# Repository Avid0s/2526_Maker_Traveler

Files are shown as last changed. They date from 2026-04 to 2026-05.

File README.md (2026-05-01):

# 25-26_Maker_Traveler
Gabriel VIDON\
Projet d'option Maker à l'ENSEA.

# Vidéo :
Version 1 min 30 :\
https://youtu.be/IOBbxCDs6Es

Version 1 min 45 : (une étape en plus)\
https://youtu.be/CtQkx19j3xo

# 1 Description du projet

## 1.1 Contexte

J'ai toujours été passioné par la robotique et les systèmes embarqués, c'est pour cela que dans le cadre d'un projet Maker qui devait regrouper le plus de technologies possibles pour apprendre leur fonctionnement. J'ai décidé de travailler sur un projet de voiture téléguidée par connection bluetooth. Pour éviter de devoir créer un système de rotation pour les roues de zero, j'ai décidé d'utiliser des roues holonomes.\ 
Ce système qui deverait toucher à toutes les technologies d'impression 3D, de découpe laser, routage pcb, et toutes les autres vues en cours de Maker.
Mes objectifs sont les suivants :
- Créer un chassis pouvant supporter l'ensemble du système
- Créer un PCB avec un ESP32 permettant de controler les moteurs
- Créer un programme permettant de communiquer en bluetooth avec l'ESP et de controler la voiture depuis un telephone puis une manette.

## 1.2 Retroplanning

| Séance | Objectif|
|---|---|
|TP1 |Définir les spécifications, choisir les composants, rédiger le cahier des charges et planifier les tâches.|
|TP2 |Modéliser le châssis en 3D, concevoir le schéma du PCB et préparer les fichiers pour la fabrication.|
|TP3 |Imprimer/découper le châssis, finaliser le PCB et préparer les outils pour la séance suivante.|
|TP4 |Souder les composants sur le PCB et écrire le code de base pour contrôler les moteurs.|
|TP5 |Développer la communication Bluetooth et tester les mouvements de la voiture.|
|TP6 |Assembler le châssis, tester l'ensemble (mouvements, Bluetooth) et finaliser le code.|
|TP7 |Valider les tests, rédiger le rapport technique et préparer la démonstration.|

# 2 Projet

## Séance 1

L'alimentation de la voiture sera fait grâce a une batterie 12v, cette tension sera convertie en 5v par un convertisseur DC-DC, qui alimentera toute la carte.\
Un esp32 recuperera les informations de mouvement depuis une connection bluetooth, enverra la PWM appropriée aux drivers, qui eux controleront les moteurs.\
Les moteurs seront eux alimentés par la batterie 12v, et leur valeur d'encodeur sera renvoyée à l'esp pour permettre un niveau de précision adéquat pour utiliser les roues omnidirectionelles.\
Une interface sera faite sur telephone avec l'application BT electronics, et si le temps le permets, le robot sera controlé par une manette de ps4

| Composant | Référence | Lien | Quantité |
|---|---|---|---|
| Moteurs | FIT0520 | [https://www.dfrobot.com/product-1619.html](https://www.dfrobot.com/product-1619.html)| x4 |
| Drivers moteur | DRV8411APWPR | | x2 |
| ESP32 | | | x1 |
| Roues omnidirectionelles | FIT0779 | [https://www.gotronic.fr/art-roue-omnidirectionnelle-droite-fit0780-34179.htm](https://www.gotronic.fr/art-roue-omnidirectionnelle-droite-fit0780-34179.htm) | x2L x2R |
| Convertisseur 6v-5v | 171013801 | [https://www.we-online.com/components/products/datasheet/171013801.pdf](https://www.we-online.com/components/products/datasheet/171013801.pdf) | x1 |
| Batterie 6v | fait in ensea |  | x1 |

Lien Onshape :\
[https://cad.onshape.com/documents/018aeca4da422949587763ea/w/2b34d823b7b37a4e9442f19b/e/016c48b2dd776d725fede060](https://cad.onshape.com/documents/018aeca4da422949587763ea/w/2b34d823b7b37a4e9442f19b/e/016c48b2dd776d725fede060)

traveler

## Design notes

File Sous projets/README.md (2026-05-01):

# Onshape CAD
screw_box_thing
phone_holder
spring
joint_thing
useless_box

# Impression 3D
Weaponised_benchy

# Découpe laser
https://github.com/user-attachments/assets/71cb4131-c118-4ef8-b6b2-2d7144401bef

# Routage PCB
Je me rappelle d'avoir fait la majorité du travail demandé pour cet exercice, mais je ne retrouve pas le document KiCad. Je peux en échange vous montrer d'autres projets KiCad que j'ai faits depuis.

https://github.com/Spoyke/Nomad/tree/main/PCBs/Commande
schema_elec_nomad
routage_nomad
Voici la version finale de mon PCB de projet de 2A, qui a été refait à plusieurs reprises.

https://github.com/Avid0s/2526_Maker_Traveler/tree/main/PCB/Traveler_v2
Vous pouvez aussi voir mon PCB de ce projet sur ce git

Et même le routage que j'ai fait durant mon stage de BUT2
Zuken_CR-5000
Zuken_CR-5000_part2
L'application utilisée est [CR-5000 de Zuken](https://en.wikipedia.org/wiki/CR-5000)

# Soudure PCB
Nous n'avons pas pris de photos du PCB et nous ne le retrouvons plus maintenant :(

# Couture
Couture_v1
Couture_v2

# Batteries
Je n'ai pas pris de photos de la batterie non plus. J'avais fait une batterie 3s 2p et c'est celle qui a cramé dans la boite.

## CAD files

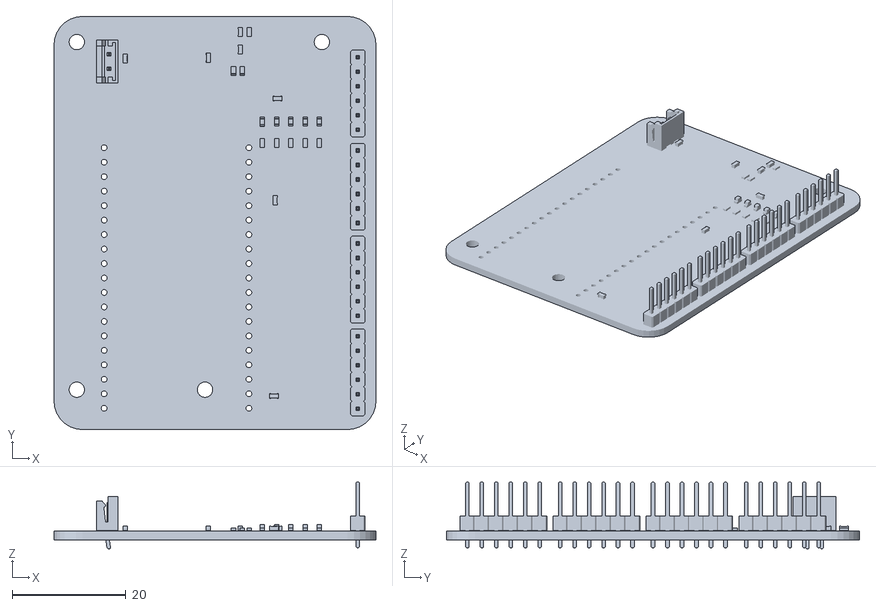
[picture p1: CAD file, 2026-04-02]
PCB/Traveler_v2/Traveler.stl
56.5 x 72.5 x 11.7

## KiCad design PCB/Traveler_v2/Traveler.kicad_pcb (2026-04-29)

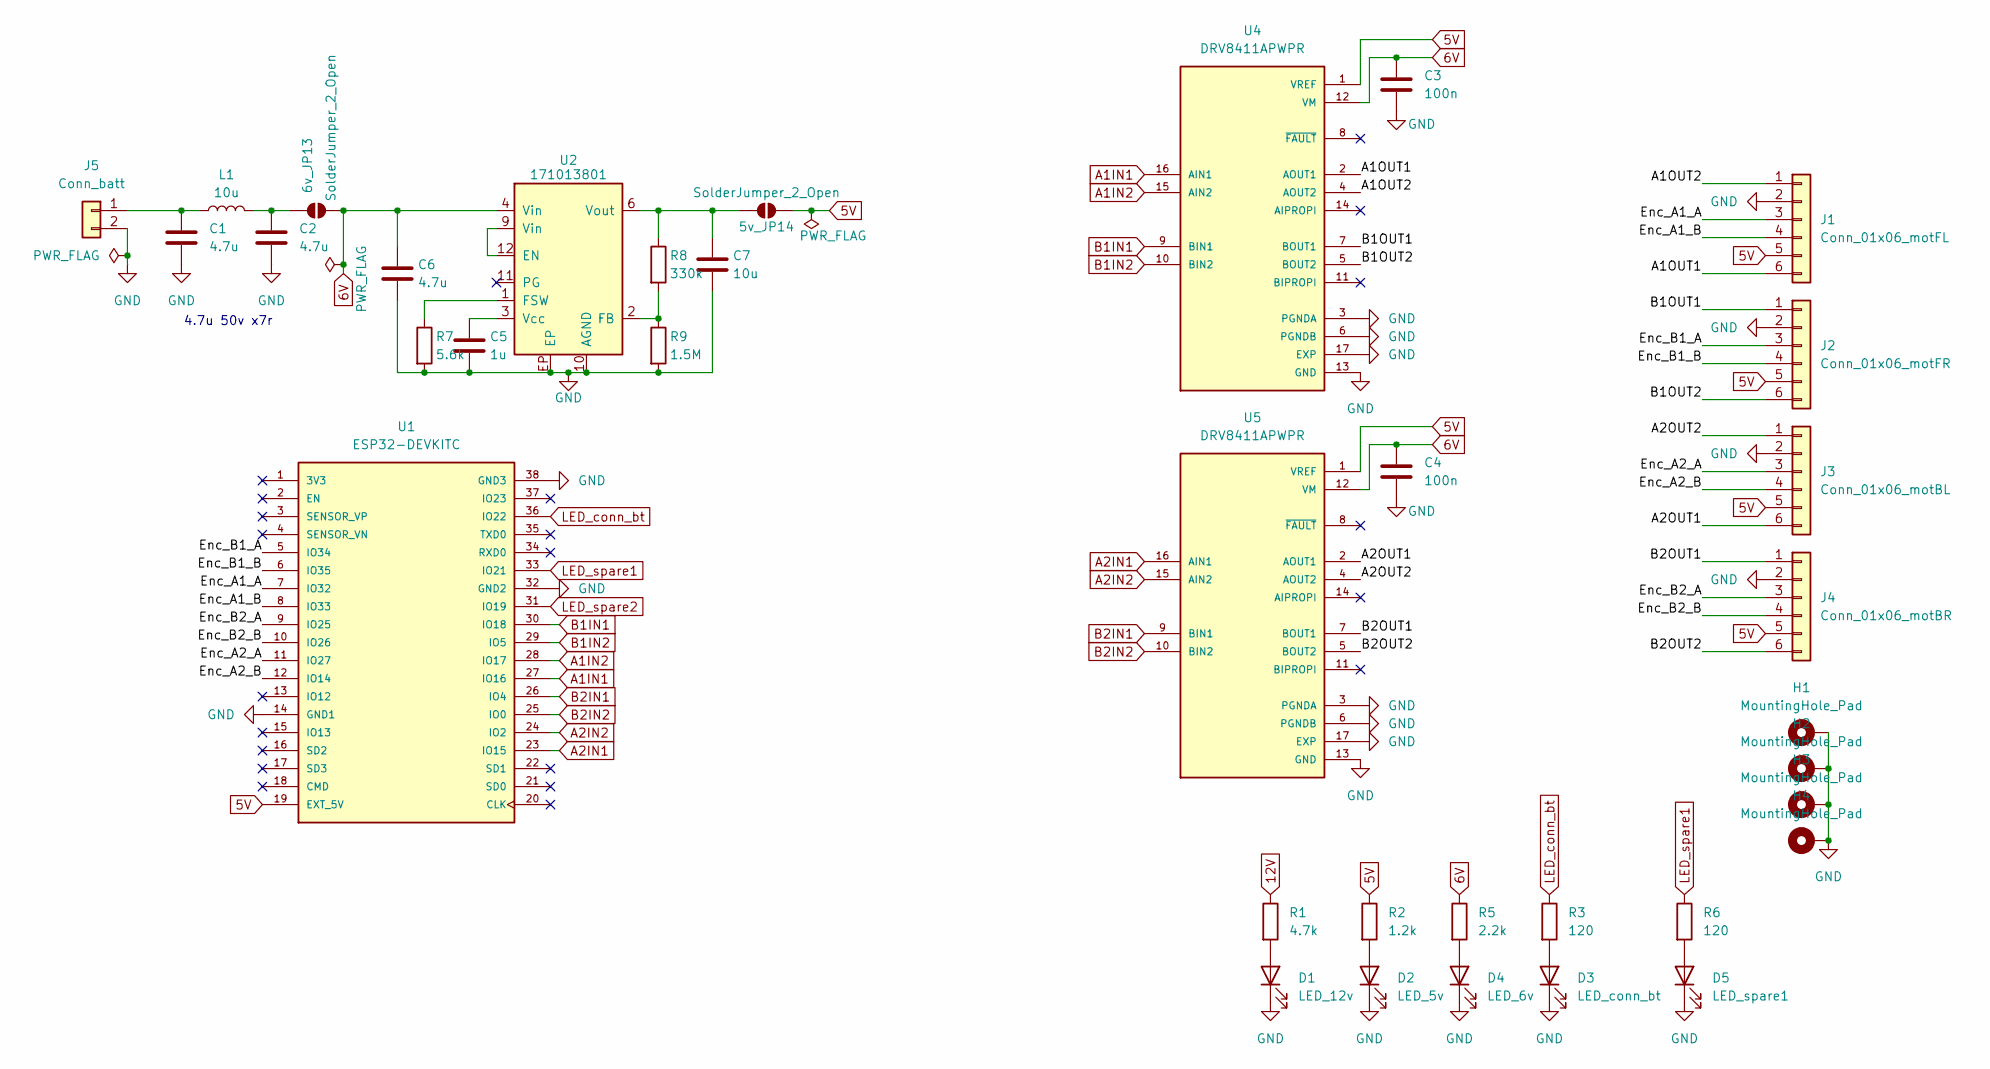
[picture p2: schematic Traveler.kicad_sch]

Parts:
5v_JP14, 6v_JP13: SolderJumper_2_Open; SolderJumper-2_P1.3mm_Open_TrianglePad1.0x1.5mm
C1, C2, C6: 4.7u; C_0603_1608Metric
C3, C4: 100n; C_0603_1608Metric
C5: 1u; C_0603_1608Metric
C7: 10u; C_0603_1608Metric
D1: LED_12v; LED_0603_1608Metric_Pad1.05x0.95mm_HandSolder
D2: LED_5v; LED_0603_1608Metric_Pad1.05x0.95mm_HandSolder
D3: LED_conn_bt; LED_0603_1608Metric_Pad1.05x0.95mm_HandSolder
D4: LED_6v; LED_0603_1608Metric_Pad1.05x0.95mm_HandSolder
D5: LED_spare1; LED_0603_1608Metric_Pad1.05x0.95mm_HandSolder
H1, H2, H3, H4: MountingHole_Pad; MountingHole_2.7mm_Pad_TopBottom
J1: Conn_01x06_motFL; PinHeader_1x06_P2.54mm_Vertical
J2: Conn_01x06_motFR; PinHeader_1x06_P2.54mm_Vertical
J3: Conn_01x06_motBL; PinHeader_1x06_P2.54mm_Vertical
J4: Conn_01x06_motBR; PinHeader_1x06_P2.54mm_Vertical
J5: Conn_batt; JST_EH_B2B-EH-A_1x02_P2.50mm_Vertical
L1: 10u; capa1
R1: 4.7k; R_0603_1608Metric
R2: 1.2k; R_0603_1608Metric
R3, R6: 120; R_0603_1608Metric
R5: 2.2k; R_0603_1608Metric
R7: 5.6k; R_0603_1608Metric
R8: 330k; R_0603_1608Metric
R9: 1.5M; R_0603_1608Metric
U1: ESP32-DEVKITC; MODULE_ESP32-DEVKITC; PARTREV N/A
U2: 171013801; WPME-VDLM_LGA-12EP
U4, U5: DRV8411APWPR; IC_DRV8411APWPR; PARTREV A

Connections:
5V: 5v_JP14.2 (B), J1.5, J2.5, J3.5, J4.5, R2.1, U1.19 (EXT_5V), U4.1 (VREF), U5.1 (VREF)
6V: 6v_JP13.2 (B), C3.1, C4.1, C6.1, R5.1, U2.4 (Vin), U2.5 (Vin), U4.12 (VM), U5.12 (VM)
12V: R1.1
/A1OUT1: J1.6, U4.2 (AOUT1)
/A1OUT2: J1.1, U4.4 (AOUT2)
/A2OUT1: J3.6, U5.2 (AOUT1)
/A2OUT2: J3.1, U5.4 (AOUT2)
/B1OUT1: J2.1, U4.7 (BOUT1)
/B1OUT2: J2.6, U4.5 (BOUT2)
/B2OUT1: J4.1, U5.7 (BOUT1)
/B2OUT2: J4.6, U5.5 (BOUT2)
/Enc_A1_A: J1.3, U1.7 (IO32)
/Enc_A1_B: J1.4, U1.8 (IO33)
/Enc_A2_A: J3.3, U1.11 (IO27)
/Enc_A2_B: J3.4, U1.12 (IO14)
/Enc_B1_A: J2.3, U1.5 (IO34)
/Enc_B1_B: J2.4, U1.6 (IO35)
/Enc_B2_A: J4.3, U1.9 (IO25)
/Enc_B2_B: J4.4, U1.10 (IO26)
A1IN1: U1.27 (IO16), U4.16 (AIN1)
A1IN2: U1.28 (IO17), U4.15 (AIN2)
A2IN1: U1.23 (IO15), U5.16 (AIN1)
A2IN2: U1.24 (IO2), U5.15 (AIN2)
B1IN1: U1.30 (IO18), U4.9 (BIN1)
B1IN2: U1.29 (IO5), U4.10 (BIN2)
B2IN1: U1.26 (IO4), U5.9 (BIN1)
B2IN2: U1.25 (IO0), U5.10 (BIN2)
GND: C1.2, C2.2, C3.2, C4.2, C5.2, C6.2, C7.2, D1.1 (K), D2.1 (K), D3.1 (K), D4.1 (K), D5.1 (K), H1.1, H2.1, H3.1, H4.1, J1.2, J2.2, J3.2, J4.2, J5.2, R7.2, R9.2, U1.14 (GND1), U1.32 (GND2), U1.38 (GND3), U2.10 (AGND), U2.EP, U4.3 (PGNDA), U4.6 (PGNDB), U4.13 (GND), U4.17 (EXP), U5.3 (PGNDA), U5.6 (PGNDB), U5.13 (GND), U5.17 (EXP)
LED_conn_bt: R3.1, U1.36 (IO22)
LED_spare1: R6.1, U1.33 (IO21)
LED_spare2: U1.31 (IO19)
unnamed: 6v_JP13.1 (A), C2.1, L1.2
unnamed: D1.2 (A), R1.2
unnamed: D2.2 (A), R2.2
unnamed: D3.2 (A), R3.2
unnamed: D4.2 (A), R5.2
unnamed: D5.2 (A), R6.2
unnamed: C1.1, J5.1, L1.1
unnamed: U2.9 (Vin), U2.12 (EN)
unnamed: R8.2, R9.1, U2.2 (FB)
unnamed: R7.1, U2.1 (FSW)
unnamed: C5.1, U2.3 (Vcc)
Vout: 5v_JP14.1 (A), C7.1, R8.1, U2.6 (Vout), U2.7 (Vout)

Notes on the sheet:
4.7u 50v x7r

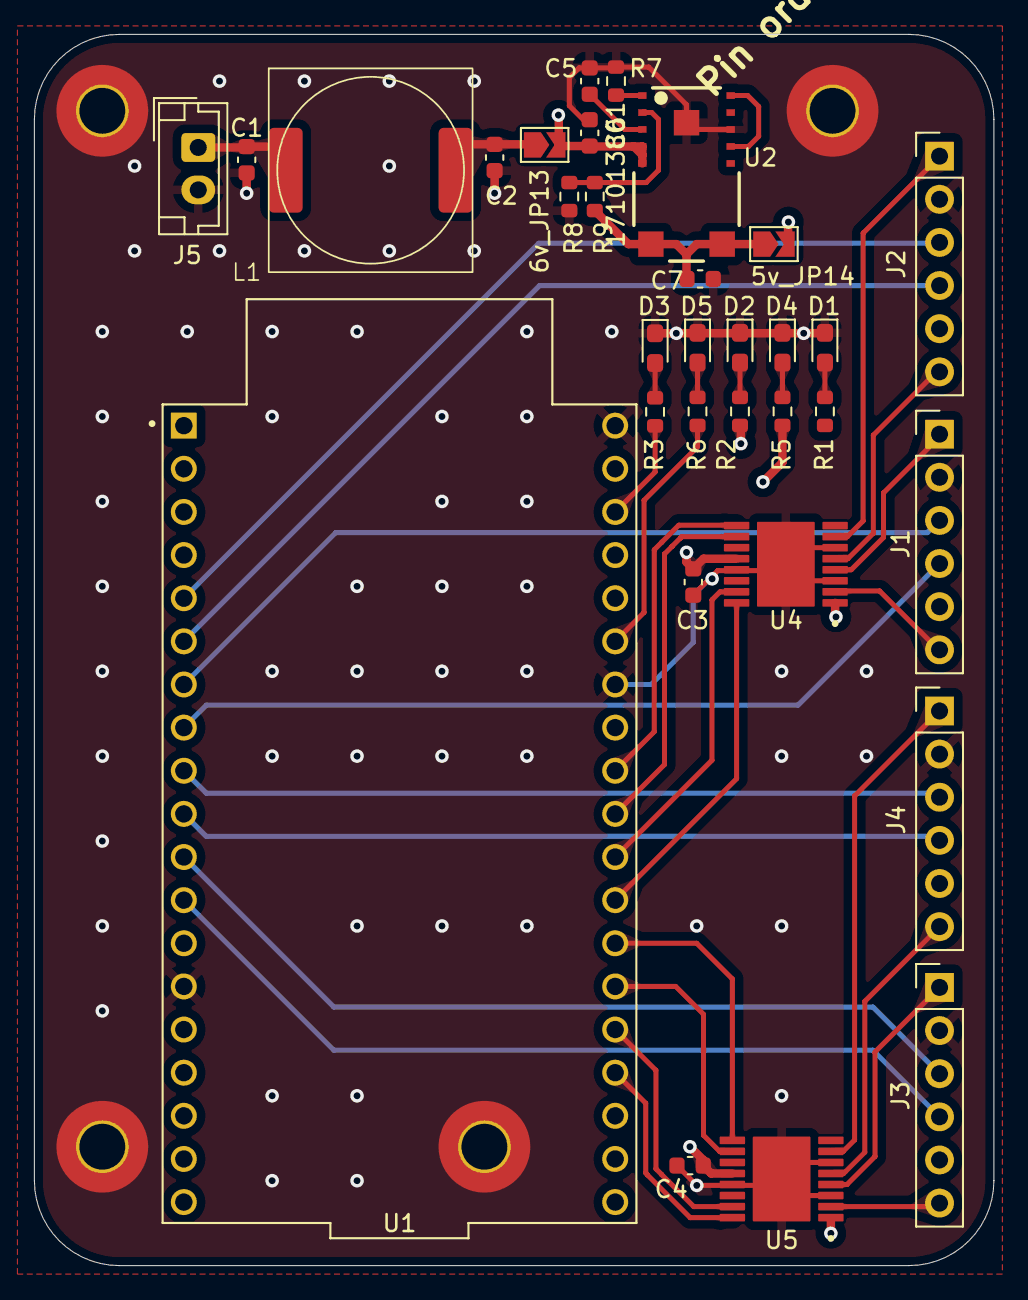
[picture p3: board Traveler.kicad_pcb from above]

Board: 4 copper layers, 56.5 x 72.5 mm, 36 parts (0 on the bottom side), 41 nets.

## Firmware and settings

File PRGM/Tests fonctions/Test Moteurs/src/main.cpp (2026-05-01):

#include <Arduino.h>
#include <BluetoothSerial.h>
#include <string.h>

struct Motor{
  int IN1;
  int IN2;
  int C1;
  int C2;
};

//function declarations
void forward(Motor motor);
void backward(Motor motor);
void stop(Motor motor);

struct Motor motorFL = {16, 17, 32, 33}; // Initialize motor structure
struct Motor motorFR = {5, 18, 34, 35}; 
struct Motor motorBR = {0, 4, 25, 26};
struct Motor motorBL = {15, 2, 27, 14};

uint16_t RxValue = 0;    // Initialisation de la valeur de reception
uint8_t buffer[100]; // Initialisation d'un buffer de 100 octets

BluetoothSerial SerialBT;

void setup() {
  Serial.begin(115200);
  delay(1000); // Give serial time to initialize

  Serial.println("Starting ESP32 Bluetooth...");

  pinMode(22, OUTPUT);

  pinMode(motorFL.IN1, OUTPUT);
  pinMode(motorFL.IN2, OUTPUT);
  pinMode(motorFR.IN1, OUTPUT);
  pinMode(motorFR.IN2, OUTPUT);
  pinMode(motorBR.IN1, OUTPUT);
  pinMode(motorBR.IN2, OUTPUT);
  pinMode(motorBL.IN1, OUTPUT);
  pinMode(motorBL.IN2, OUTPUT);

  // Initialize Bluetooth - slave mode to accept connections from phone
  bool btStarted = SerialBT.begin("ESP32_BT");
  Serial.print("BT Start: ");
  Serial.println(btStarted ? "OK" : "FAILED");
  
  SerialBT.setPin("1234"); // Set PIN code
  Serial.println("PIN set to: 1234");
  
  Serial.println("Bluetooth ready - search for ESP32_BT on your device");

  // Check connection status
  do{
    if (SerialBT.hasClient()) {
      Serial.println("Phone connected!");
    }
    else {
      Serial.println("Waiting for phone to connect...");
      delay(500);
    }
  } while (!SerialBT.hasClient());
  Serial.println("Setup finished.");

}

void loop() {

  if (SerialBT.hasClient()) { //Connection check
    digitalWrite(22, HIGH);
  }
  else {
    digitalWrite(22, LOW);
  }
  
  // Check if Bluetooth data is available (at least 1 char)
  int btAvail = SerialBT.available();
  if (btAvail >= 1) {
    delay(30); // Wait for data to arrive
    // Clear buffer first to avoid garbage
    memset(buffer, 0, sizeof(buffer));
    
    // Read all available bytes
    int i = 0;
    while (SerialBT.available() && i < 98) {
      int c = SerialBT.read();
      
      if (c == 10 || c == 13) {  // Newline or CR - skip but mark as command
        break;  // Stop reading on terminator
      } else if ((c >= 65 && c <= 90) || (c >= 97 && c <= 122)) {  // A-Z or a-z
        buffer[i++] = (char)c;
      } else if (c >= 48 && c <= 57) {  // 0-9 digits
        buffer[i++] = (char)c;
      }
      // Skip everything else
    }
    
    // Flush any remaining data in buffer
    while (SerialBT.available()) {
      SerialBT.read();
    }
    
    // Process if we got valid characters
    if (i > 0) {
      buffer[i] = '\0';
      Serial.print("Cmd: ");
      Serial.println((char*)buffer);

      // Handle commands
      // First, stop all motors before changing direction or continuing
      stop(motorFL);
      stop(motorFR);
      stop(motorBR);
      stop(motorBL);

      if (strcmp((char*)buffer, "F") == 0) {
        forward(motorFL);
        forward(motorFR);
        forward(motorBR);
        forward(motorBL);
        Serial.println("Moving Forward");
      } else if (strcmp((char*)buffer, "B") == 0) {
        backward(motorFL);
        backward(motorFR);
        backward(motorBR);
        backward(motorBL);
        Serial.println("Moving Backward");
      } else if (strcmp((char*)buffer, "TL") == 0) {
        forward(motorFR);
        forward(motorBR);
        backward(motorFL);
        backward(motorBL);
        Serial.println("Turning Left");
      } else if (strcmp((char*)buffer, "TR") == 0) {
        backward(motorFR);
        backward(motorBR);
        forward(motorFL);
        forward(motorBL);
        Serial.println("Turning Right");
      } else if (strcmp((char*)buffer, "ML") == 0) {
        forward(motorFL);
        backward(motorFR);
        backward(motorBR);
        forward(motorBL);
        Serial.println("Moving Left");
      } else if (strcmp((char*)buffer, "MR") == 0) {
        backward(motorFL);
        forward(motorFR);
        forward(motorBR);
        backward(motorBL);
        Serial.println("Moving Right");
      } else {
        Serial.println("Unknown Command");
      }
    }
  }

}

// put function definitions here:
void forward(Motor motor) {
  digitalWrite(motor.IN1, LOW);
  digitalWrite(motor.IN2, HIGH); // Setting to spin in one direction
}

void backward(Motor motor) {
  digitalWrite(motor.IN1, HIGH);
  digitalWrite(motor.IN2, LOW); // Setting to spin in the opposite direction
}

void stop(Motor motor) {
  digitalWrite(motor.IN1, LOW);
  digitalWrite(motor.IN2, LOW); // Stop the motor
}

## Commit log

2026-02-16 Added séance 1
    Added project details including power supply, motor control, and components list.
2026-03-09 added ref driver moteur
2026-03-09 début schéma elec pcb
    recherches sur moteurs, drivers, esp and more
    [Traveler.kicad_pcb, Traveler.kicad_sch]
2026-03-19 Finition de pcb, prèt pour verification
    [Traveler.kicad_pcb, Traveler.kicad_sch]
2026-03-23 Vers 2 couches
    A créer : une vers 4 couches, remplacer batt 12v vers 6v pour alim directement depuis batt
    [Traveler.kicad_pcb]
2026-03-23 changements schematic elec pour une batt 6v
    a faire, routage :(
    [Traveler.kicad_pcb, Traveler.kicad_sch]
2026-03-23 Finition PCB et envoi vers fabrication
    [Traveler-B_Cu.gbr, Traveler-B_Mask.gbr, Traveler-B_Paste.gbr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]
2026-03-24 fichiers gerber et suppression backups
2026-03-30 cration of cad pcb file
2026-03-30 changement composants vers mot 6V + rajout liens
2026-04-02 Remove Traveler.cad; add backups, STL, lock
    Delete the large Traveler.cad export and update the KiCad project metadata. Add two backup ZIPs in PCB/Traveler_v2/Traveler-backups, include Traveler.stl and the temporary ~Traveler.kicad_pcb.lck loc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
    [Traveler.stl]
2026-04-13 erreur avec le ldo, ordre des pins inversé sur KiCad, composant à souder en araignée
    [Traveler.kicad_pcb, Traveler.kicad_sch]
2026-04-29 Code moteurs
    [Traveler.kicad_pcb]
2026-04-29 prgm, pour de vrai
    code BT et fonctions moteurs
2026-05-01 petites modifs code et kicad
